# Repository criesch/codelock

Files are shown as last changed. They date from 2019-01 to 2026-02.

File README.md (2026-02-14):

# Codelock

This is a code lock for house doors, garage openers etc.

## Required Hardware

I use this piece of code on
* an Arduino UNO SMD Rev 3,
* the Seeed Technology Relay Shield
* A 12 button numeric keypad (10 digits plus * and #) like the SparkFun Electronics 14662.

Digikey part numbers are
| pcs | Description | Digikey part number |
|-----|---|---|
| 1 | Arduino UNO SMD Rev 3 | 1050-1041-ND |
| 1 | Seed Technology Relay Shield | 1597-1146-ND |
| 1 | SparkFun 14662 Keypad | 1568-14662-ND |

I have 3D printed a housing for the SparkFun keyboard, see the STL files in the housing
subdirectory. The housing is for the keyboard only. I mount the Arduino and the relay
shield in a box inside the building to prevent someone from bridging the relay contacts.

## Wiring

The keypad is wired to the Arduino as follows:

| keypad pin | Arduino pin | Description |
|---|---|---|
| 1 | n/a | not connected |
| 2 | 11 | column 2
| 3 | 2 | row 1
| 4 | 10 | column 1
| 5 | 9 | row 4
| 6 | 12 | column 3
| 7 | 8 | row 3
| 8 | 3 | row 2
| 9 | n/a | not connected |

## Usage

Type the code and push the # key to close relay 1 for two seconds. The other
3 relays (to open e.g. the garage door instead of the house door) can be addressed
by typing N*code#, where N is the number of the relay 1-4. Also adressing of
several relays at the same time is possible, as configured in the
variable relaySets. The relays are then operated in a sequence, one after the other.

The code is hardcoded in the variable CODE.

## License

code lock

Copyright (c) 2019-2026 Christian Riesch, christian@riesch.at

Permission to use, copy, modify, and/or distribute this software for any
purpose with or without fee is hereby granted, provided that the above
copyright notice and this permission notice appear in all copies.

THE SOFTWARE IS PROVIDED "AS IS" AND THE AUTHOR DISCLAIMS ALL WARRANTIES
WITH REGARD TO THIS SOFTWARE INCLUDING ALL IMPLIED WARRANTIES OF
MERCHANTABILITY AND FITNESS. IN NO EVENT SHALL THE AUTHOR BE LIABLE FOR ANY
SPECIAL, DIRECT, INDIRECT, OR CONSEQUENTIAL DAMAGES OR ANY DAMAGES
WHATSOEVER RESULTING FROM LOSS OF USE, DATA OR PROFITS, WHETHER IN AN
ACTION OF CONTRACT, NEGLIGENCE OR OTHER TORTIOUS ACTION, ARISING OUT OF OR
IN CONNECTION WITH THE USE OR PERFORMANCE OF THIS SOFTWARE.

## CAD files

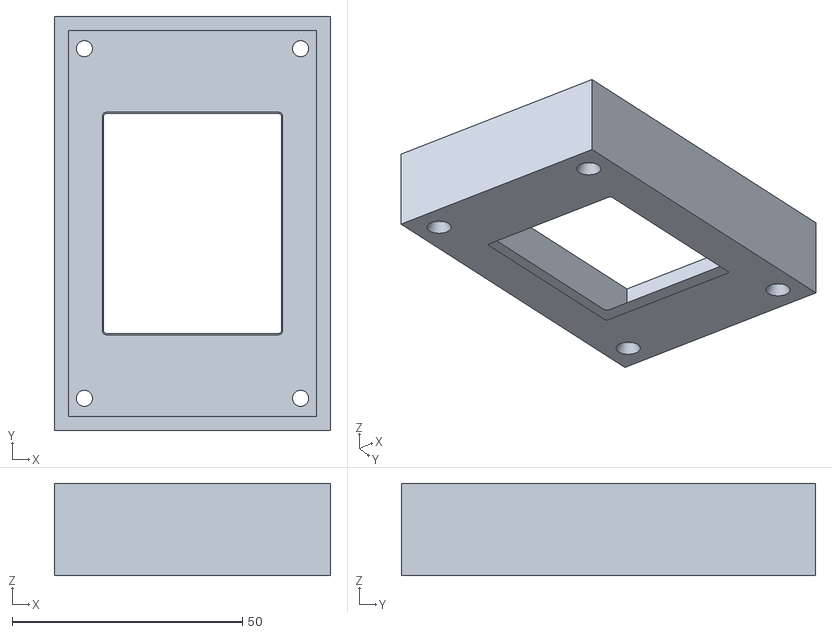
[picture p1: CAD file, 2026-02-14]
housing/Keyboard-Frame.stl
60.0 x 90.0 x 20.0

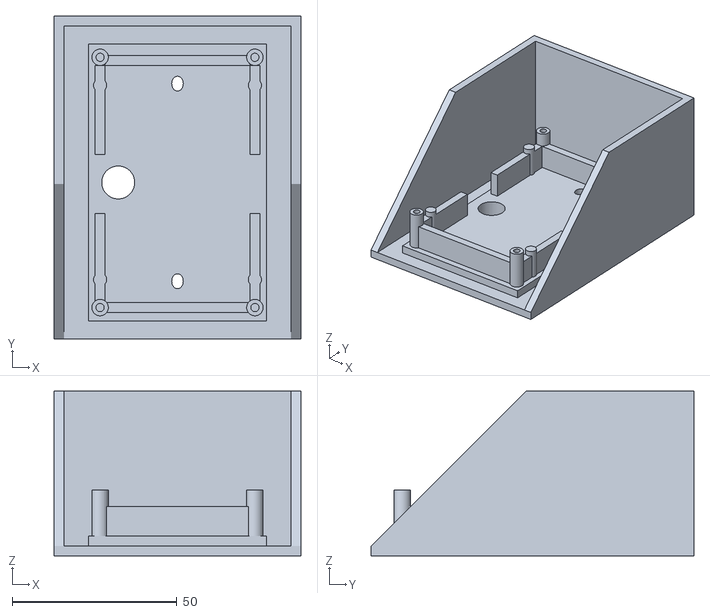
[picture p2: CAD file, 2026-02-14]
housing/Keyboard-Base.stl
75.0 x 98.0 x 50.0

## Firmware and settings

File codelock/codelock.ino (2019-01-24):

/*
 * code lock
 *
 * Copyright (c) 2019 Christian Riesch, christian@riesch.at
 *
 * Permission to use, copy, modify, and/or distribute this software for any
 * purpose with or without fee is hereby granted, provided that the above
 * copyright notice and this permission notice appear in all copies.
 *
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
 */

#include <Keypad.h>

// keypad definition
const byte ROWS = 4; //four rows
const byte COLS = 3; //three columns

char keys[ROWS][COLS] = {
  {'1','2','3'},
  {'4','5','6'},
  {'7','8','9'},
  {'*','0','#'}
};

byte rowPins[ROWS] = {2, 3, 8, 9}; //connect to the row pinouts of the keypad
byte colPins[COLS] = {10, 11, 12}; //connect to the column pinouts of the keypad

Keypad keypad = Keypad( makeKeymap(keys), rowPins, colPins, ROWS, COLS );

// output relays
const byte NUMRELAYS = 4;
byte relaypins[NUMRELAYS] = { 7, 6, 5, 4 };
const byte defaultRelay = 1 << 0;

// relay selection, pressing 0* before the code selects the relays defined in relaySets[0],
// pressing 1* selects those in relaySets[1] etc.
byte relaySets[10] = { 0x01, 0x01, 0x02, 0x04, 0x08, 0x03, 0x0b, 0x0f, 0x01, 0x01 };

const unsigned long BUFFERTIMEOUT = 5000;
const unsigned long RELAYONTIME = 2000;

// code buffer
const char CODE[] = "12345";
const byte MAXCODELENGTH = 10;
String codeBuf = "";

// keyboard timeout
unsigned long lastkeypresstime = 0;

// relays selection and unlocking
byte selectedRelay = defaultRelay;
byte unlockedRelay = 0;

// relay operation
unsigned long relayActivationTime;
int activeRelay = -1;

// relay 1 push button
byte pinRelay1Pb = 13;

// fail counter: lock all relays for X milliseconds after Y failed attempts
const byte LOCKOUT_THRESHOLD = 3;
const unsigned long LOCKOUT_DURATION = 60000;
byte lockoutCnt = 0;
unsigned long lockoutTime = 0;

void setup() {
  Serial.begin(9600);

  clearbuf();

  for (byte i = 0; i < NUMRELAYS; i++) {
    digitalWrite(relaypins[i], LOW);
    pinMode(relaypins[i], OUTPUT);
  }
  pinMode(pinRelay1Pb, INPUT_PULLUP);

  Serial.println("starting...");
}

void loop() {
  // handle buffer timeout, if no key was pressed in the last BUFFERTIMEOUT
  // milliseconds, clear the code buffer and select the default relay
  if ((millis() - lastkeypresstime) > BUFFERTIMEOUT) {
    if (codeBuf.length() != 0) {
      Serial.println("buffer timeout: clear buffer");
      clearbuf();
    }
    if (selectedRelay != defaultRelay) {
      selectedRelay = defaultRelay;
      Serial.println("buffer timeout: select relays 0x" + String(selectedRelay, HEX));
    }
  }

  // reset the lockout counter after LOCKOUT_DURATION time
  if (((millis() - lockoutTime) > LOCKOUT_DURATION) && (lockoutCnt > 0)) {
    Serial.println("lockout: Reset lockout counter");
    lockoutCnt = 0;
  }

  // check the dedicated second relay pushbutton. Pressing this button selects
  // the second relay.
  if ((lockoutCnt < LOCKOUT_THRESHOLD) && (digitalRead(pinRelay1Pb) == LOW)) {
    lastkeypresstime = millis();
    if (selectedRelay != (1 << 1)) {
      selectedRelay = (1 << 1);
      Serial.println("pushbutton: select relay 0x" + String(selectedRelay, HEX));
    }
  }

  // handle keyboard events
  char key;
  if (lockoutCnt < LOCKOUT_THRESHOLD) {
    key = keypad.getKey();
  } else {
    key = NO_KEY;
  }

  if (key != NO_KEY){
    Serial.println(key);

    switch(key) {
      case '#':
        // verify code
        if (isCodeGood()) {
          Serial.println("unlocking relays 0x" + String(selectedRelay, HEX));
          unlockedRelay |= selectedRelay;
          selectedRelay = defaultRelay;
          lockoutCnt = 0;
        } else {
          Serial.println("#: wrong code entered.");
          lockoutCnt++;
          lockoutTime = millis();
        }
        clearbuf();
        break;
      case '*':
        // relay selection, select one of the relay sets defined in relaySets[]
        if (codeBuf.length() == 1) {
          // only if a single key is in the buffer
          if ((codeBuf.charAt(0) >= '0') && (codeBuf.charAt(0) <= '9')) {
            selectedRelay = relaySets[codeBuf.charAt(0) - '0'];
            Serial.println("*: select relays 0x" + String(selectedRelay, HEX));
          }
        }
        clearbuf();
        break;
      default:
        // any other key is just added to the buffer
        pushkey(key);
        break;
    }
    lastkeypresstime = millis();
  }

  // operate the relays when they are unlocked in the unlockedRelay bit field
  if (activeRelay >= 0) {
    // currently one relay is in on state, switch it off after RELAYONTIME
    if (millis() - relayActivationTime > RELAYONTIME) {
      digitalWrite(relaypins[activeRelay], LOW);
      Serial.println("relay: switch off relay " + String(activeRelay));
      unlockedRelay &= ~(1 << activeRelay); // clear bit
      activeRelay = -1;
    }
  } else {
    // no relay in on state, check if there is an unlocked one
    for (byte i = 0; i < NUMRELAYS; i++) {
      if (unlockedRelay & (1 << i)) { // test bit
        digitalWrite(relaypins[i], HIGH);
        Serial.println("relay: switch on relay " + String(i));
        relayActivationTime = millis();
        activeRelay = i;
        break; // exit loop, we only have one relay in on state at a time
      }
    }
  }
}

void clearbuf()
{
  codeBuf = "";
}

void pushkey(char c)
{
  if (codeBuf.length() < MAXCODELENGTH)
    codeBuf += String(c);
}

bool isCodeGood()
{
  if (codeBuf == CODE) {
    return true;
  } else {
    return false;
  }
}

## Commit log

2019-01-22 Enable "select relay 1" button
    Pulling low pin 13 with a button selects relay 1.
2019-01-24 Fix order of relay pins
    [codelock.ino]
2019-01-24 Only operate one relay at a time
    Furthermore add a delay after three failed attempts to unlock.
    Allow the definition of relay sets that are unlocked together.
    [codelock.ino]
2026-02-14 Add STL files for keyboard housing
    [Keyboard-Base.stl, Keyboard-Frame.stl]
